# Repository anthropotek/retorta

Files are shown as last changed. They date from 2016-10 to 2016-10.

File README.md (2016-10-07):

# Retorta

mercury amalgam retort for gold mining

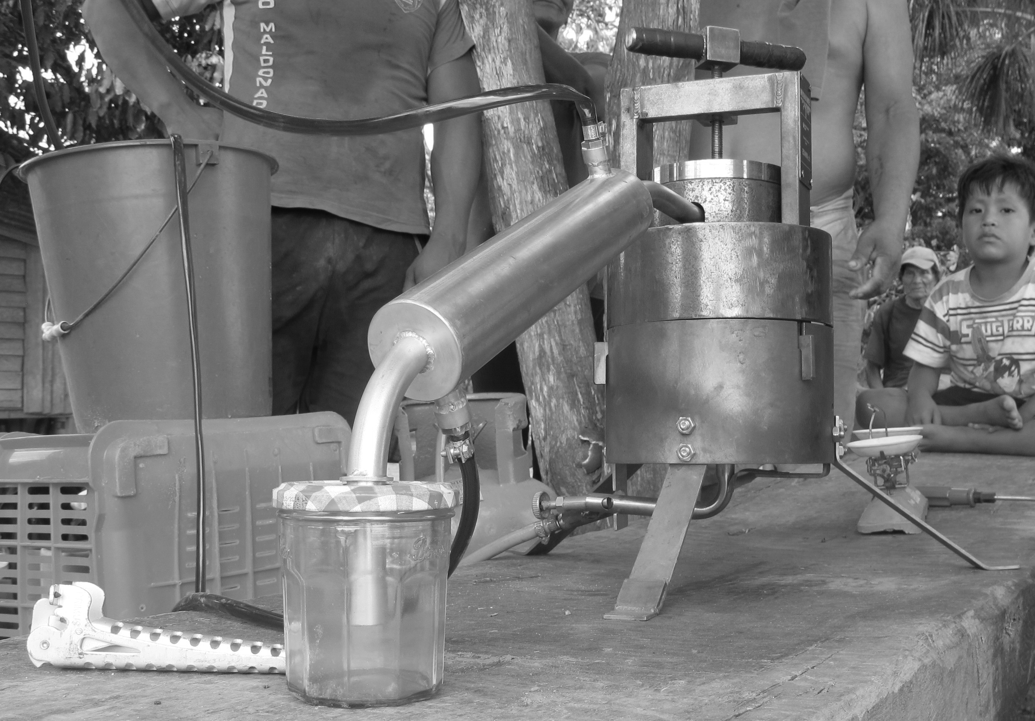
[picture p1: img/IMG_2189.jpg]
Retorta


## Getting Started

These instructions will get you a copy of the project up and running on your local machine for development and testing purposes. See deployment for notes on how to deploy the project on a live system.

### Prerequisities

What things you need to install the software and how to install them

```
Give examples
```

### Installing

A step by step series of examples that tell you have to get a development env running

Say what the step will be

```
Give the example
```

And repeat

```
until finished
```

End with an example of getting some data out of the system or using it for a little demo

## Running the tests

Explain how to run the automated tests for this system

### Break down into end to end tests

Explain what these tests test and why

```
Give an example
```

### And coding style tests

Explain what these tests test and why

```
Give an example
```

## Deployment

Add additional notes about how to deploy this on a live system

## Built With

* Dropwizard - Bla bla bla
* Maven - Maybe
* Atom - ergaerga

## Contributing

Please read [CONTRIBUTING.md](https://gist.github.com/PurpleBooth/b24679402957c63ec426) for details on our code of conduct, and the process for submitting pull requests to us.

## Versioning

We use [SemVer](http://semver.org/) for versioning. For the versions available, see the [tags on this repository](https://github.com/your/project/tags). 

## Authors
Haute Ecole Arc Engineering - Team "User-Centered Product Design", website: http://anthropotechnologie.org/
This hardware is part of Wanamei project, focusing on developing socio-technical solutions to improve current mining problematics, website of the project: http://wanamei.org/

## License

This project is licensed under the Creative Commons Licence – Attribution Non commercial – ShareAlike 3.0 Unported. This means that the retorta cannot be marketed directly and in a collaborative spirit, we ask you to share with us the modifications you might have made. See the https://creativecommons.org/licenses/by-sa/3.0/ website for details.

## Acknowledgments

* Hat tip to anyone who's code was used
* Inspiration
* etc

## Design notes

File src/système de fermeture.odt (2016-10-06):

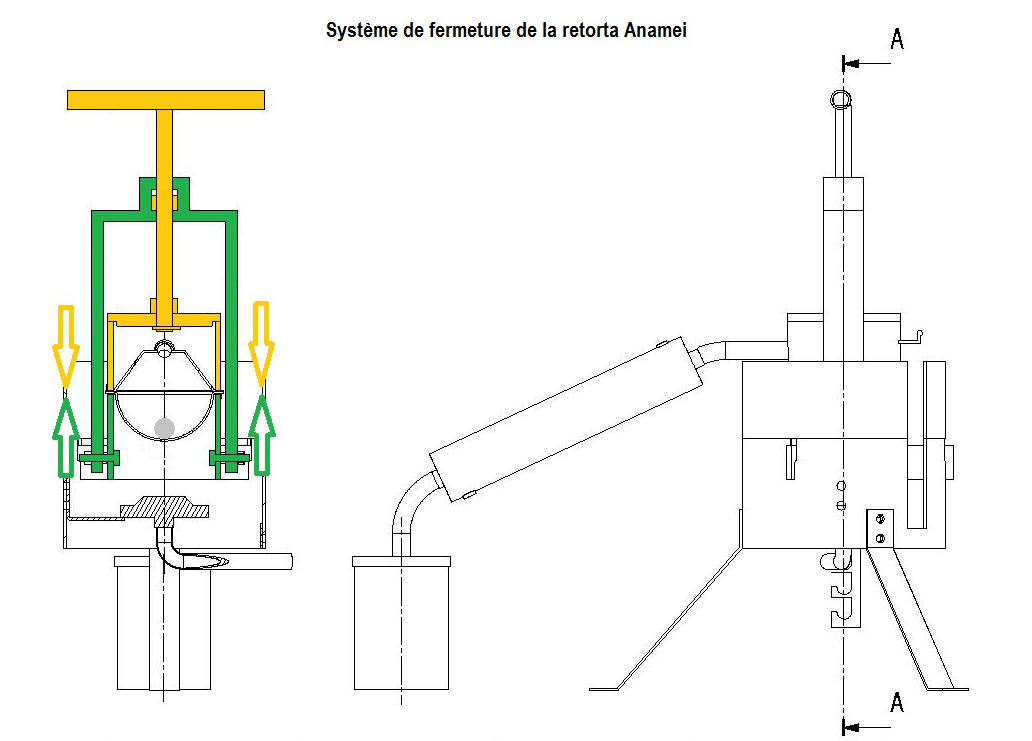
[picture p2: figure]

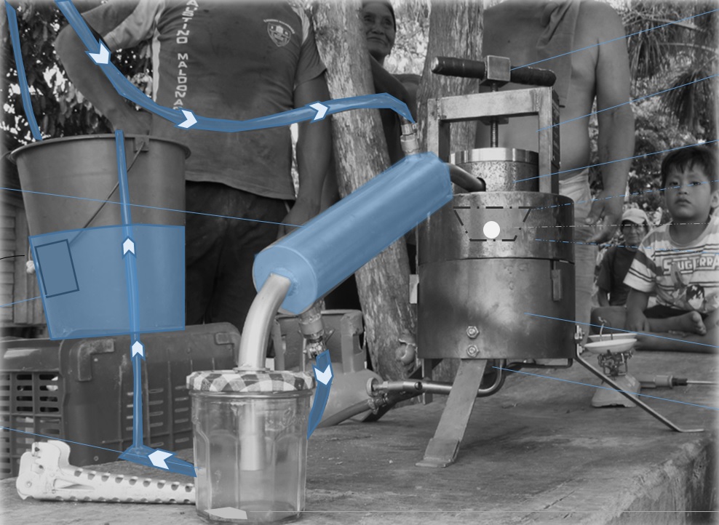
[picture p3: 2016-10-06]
img/IMG_2189 water.jpg

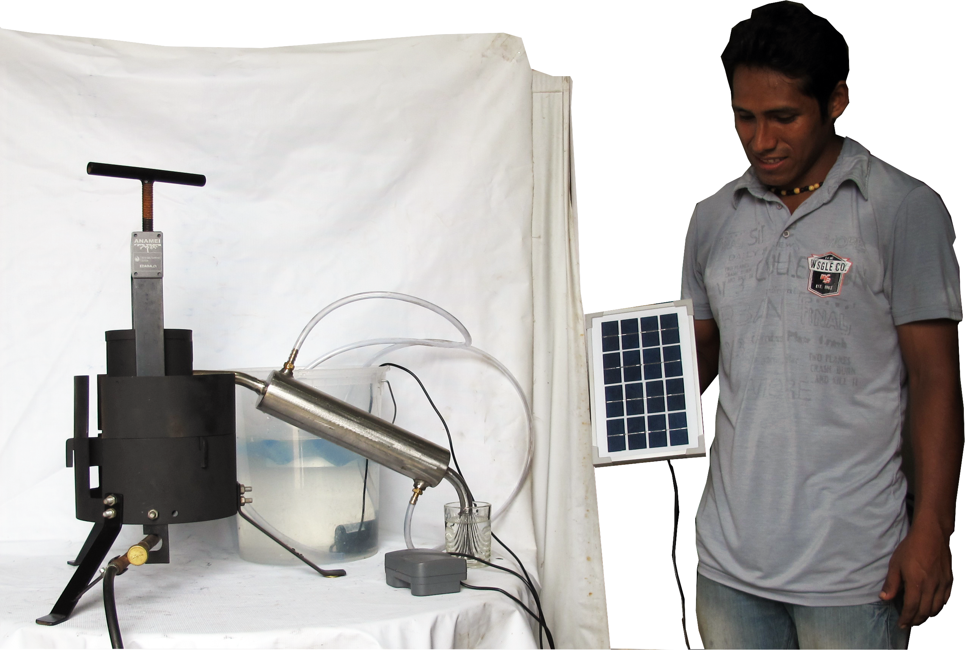
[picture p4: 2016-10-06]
img/retorta complete.png

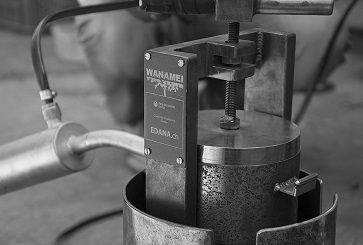
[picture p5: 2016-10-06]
img/DSC_0791pp.jpg

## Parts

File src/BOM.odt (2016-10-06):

Matériaux nécessaire à la fabrication

- Matériaux et dimensions nécessaires pour fabriquer la retorta:

Toutes les pièces sont en acier. Seul le refroidisseur est en acier inoxydable.

N° | Nom de la pièce | Photo | Matériau | Quantité
1 | Poignée | | Acier | Tube : longueur 180mm, Diamètre ext. 20mm, diamètre intérieur 10mm
2 | Tige filetée | | Acier – Degré 8 | Tige filetée : longueur 230mm, diamètre 16mm
3 | Bras | | Acier | Profil rectangulaire : 10mm*40mm, longueur : 700mm
4 | Couvercle en acier | | Acier | Plaque circulaire : diamètre 121mm, épaisseur 10mm
5 | Tube supérieur | | Acier laminé à chaud | Tube à parois épaisses, sans soudure : diamètre extérieur 121mm, diamètre intérieur 101mm, longueur 70mm
6 | Couvercle inox/ Refroidisseur inox | | Acier inoxydable 304 | Tube extérieur : diamètre extérieur 51mm, diamètre intérieur : 47mm Tube intérieur : diamètre 18mm, diamètre intérieur 16mm Plaque pour le couvercle : 600mm*185mm, épaisseur 2mm
7 | Récipient | | Aluminium / Acier inoxydable 304 | Diamètre extérieur : 120mm, rebord de 10mm, hauteur de 60mm
8 | Tube inférieur | | Acier laminé à chaud | Tube à paroi épaisse, sans soudure : diamètre extérieur 121mm, diamètre intérieur 101mm, longueur 87mm
9 | Carapace/ Armature | | Acier | Plaque de 600mm*185mm, épaisseur 3mm
10 | Pieds (*3) | | Acier | Plaque de 90mm*224mm, épaisseur 3mm (pour les 3 pieds)
11 et 12 | Supports bruleur | | Acier | Plaque de 30mm*60mm

- Type de matériau

Pour le couvercle inox/Refroidisseur inox : il est recommandé d’utiliser l’acier inoxydable AISI 304. L’inox permet de récupérer du mercure propre, non altéré ; la spécificité du n°304 est qu’il résiste aux fortes températures.

Pour les tubes supérieur et inférieur : il est recommandé d’utiliser du tube à parois épaisses, sans soudure, laminé à chaud de type : St 52.0, DIN 2448, DIN 1629.

Pour les autres pièces: il est recommandé d’utiliser de l’acier standard.

30.07.2015 wanamei.wordpress.com Guide de fabrication - Retorta Anamei

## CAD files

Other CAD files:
src/Bague stop.CATPart
src/Bol.CATPart
src/Bruleur5.CATPart
src/Couvercle bol.CATPart
src/Couvercle.CATPart
src/Cuve.CATPart
src/Echappement Retorta.CATProduct
src/Refroidisseur.CATPart
src/RetortaVF.CATProduct
src/RetortaVF2.CATProduct
src/barre.CATPart
src/carapace3.CATPart
src/carapace3_haut.CATPart
src/couvercle retorta.CATPart
src/ecrou hexa M8.CATPart
src/ecrou hexa.CATPart
src/embout 1.CATPart
src/embout 2.CATPart
src/goupille.CATPart
src/nouvel arceau.CATPart
src/pied3.CATPart
src/poignee .CATPart
src/support bruleur.CATPart
src/support soude bruleur.CATPart
src/tube bas2.CATPart
src/tube haut.CATPart
src/tube.CATPart
src/vis hexa M8 L35.CATPart

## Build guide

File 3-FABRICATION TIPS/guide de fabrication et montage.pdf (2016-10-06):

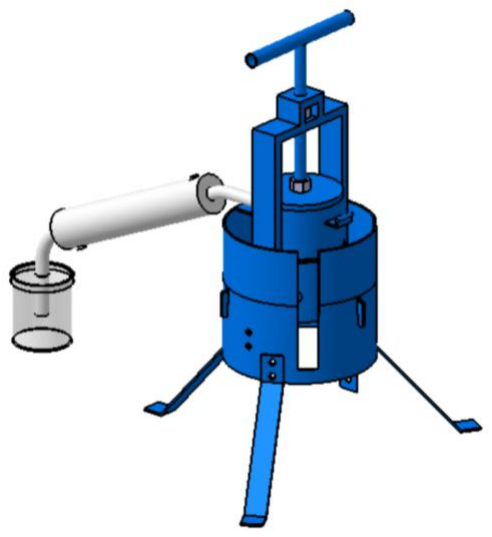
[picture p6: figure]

30.07.2015 | wanamei.wordpress.com | Guide de fabrication - Retorta Anamei

# Retorta Anamei

# Guide de fabrication et de montage

## Plan de montage

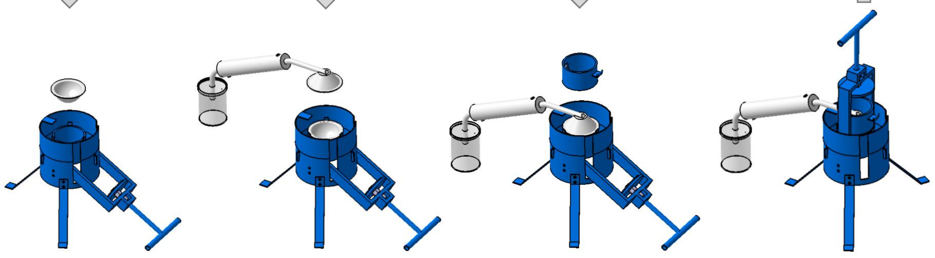
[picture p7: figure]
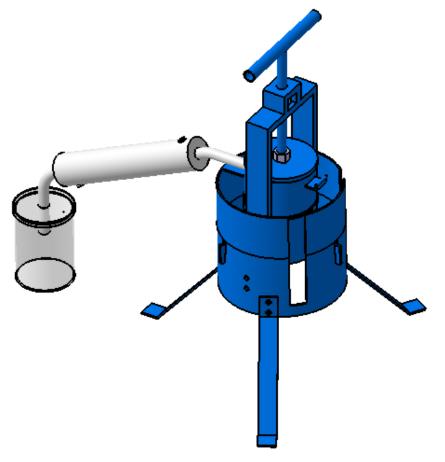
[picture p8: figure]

## Eléments de la retorta

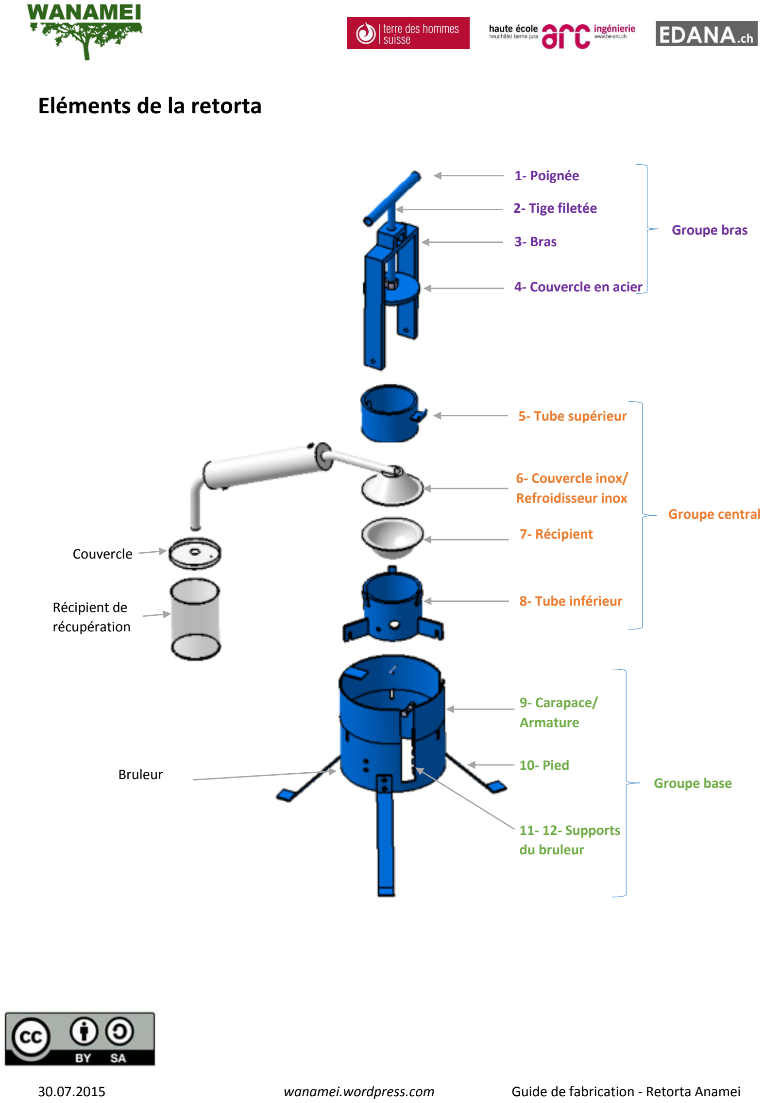
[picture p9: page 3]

Bruleur

9- Carapace/
Armature

10- Pied

Récipient de
récupération

6- Couvercle inox/
Refroidisseur inox

1- Poignée

4- Couvercle en acier

3- Bras

5- Tube supérieur

7- Récipient

8- Tube inférieur

11- 12- Supports
du bruleur

2- Tige filetée
Groupe bras

Couvercle

Groupe central

Groupe base

## Indications générales pour la fabrication

- Groupe base

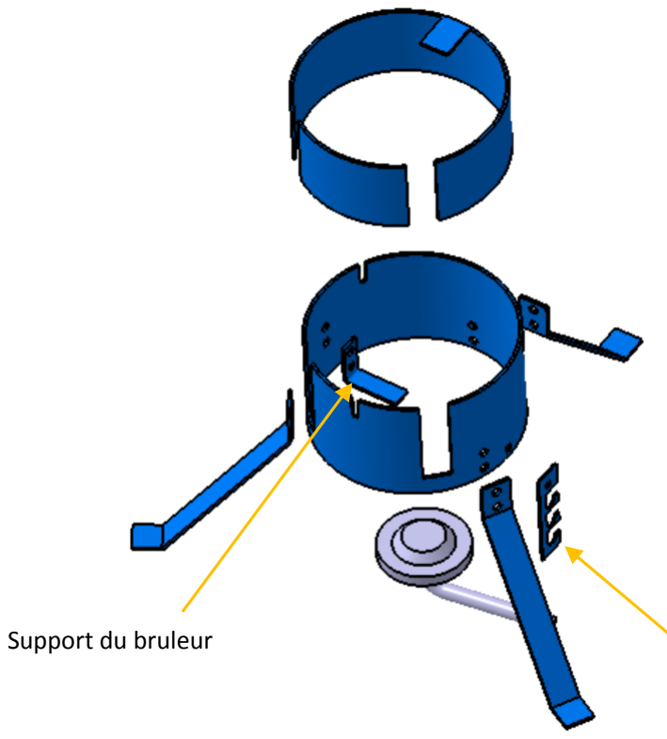
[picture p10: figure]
Support du bruleur

9 vis M8 – Longueur 16
9 écrous M8

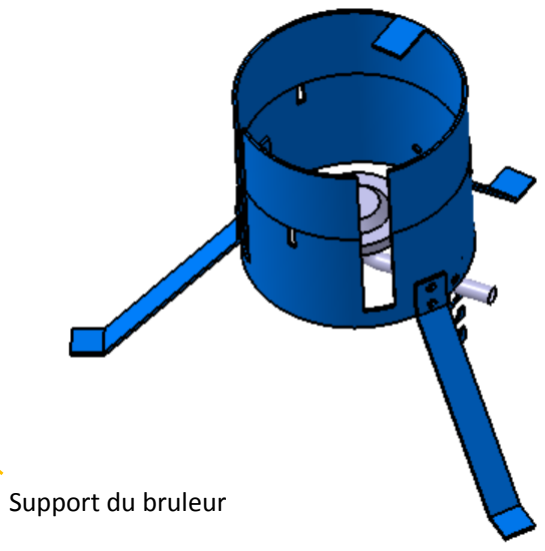
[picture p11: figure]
Support du bruleur
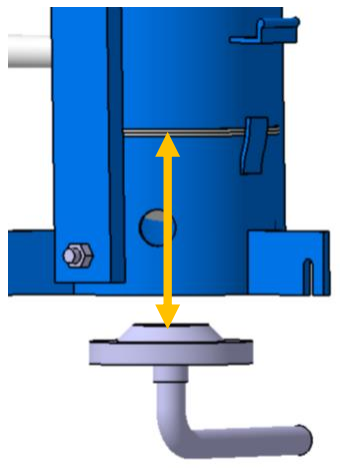
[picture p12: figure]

Distance entre le bruleur et le récipient: 90 à 100mm

- Groupe central

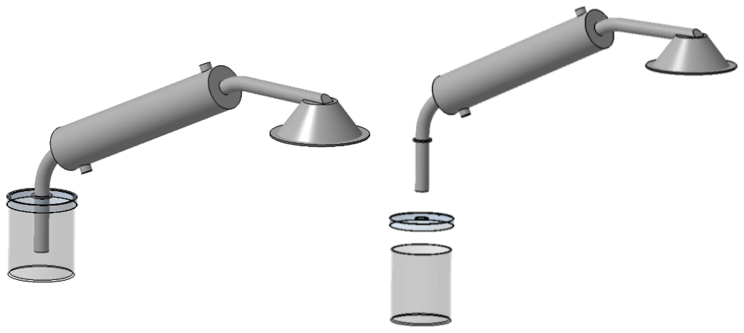
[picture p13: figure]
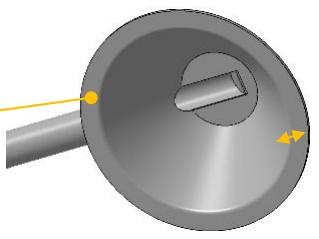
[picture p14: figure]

Notes pour la fabrication :

- Acier inoxydable 2mm d’épaisseur
- Soudure TIG
- Cette surface doit être lisse
- La largeur du rebord doit mesurer 9 mm (minimum)
- Les soudures doivent être faite à l’extérieur du couvercle.
- Cet angle doit être respecté.

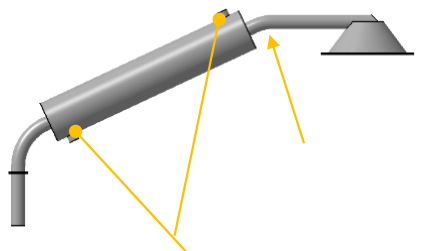
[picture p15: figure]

- Le pas de vis pour fixer les 2 connecteurs hydrauliques est : ¼.

Pour connaitre toutes les précautions de fabrication concernant la fabrication de cette pièce : voir le document « fabrication du refroidisseur » sur www.wanamei.org. (http://www.wanamei.orf/)

1 verre transparent – hauteur:135mm Trou de diamètre 18mm

9 mm

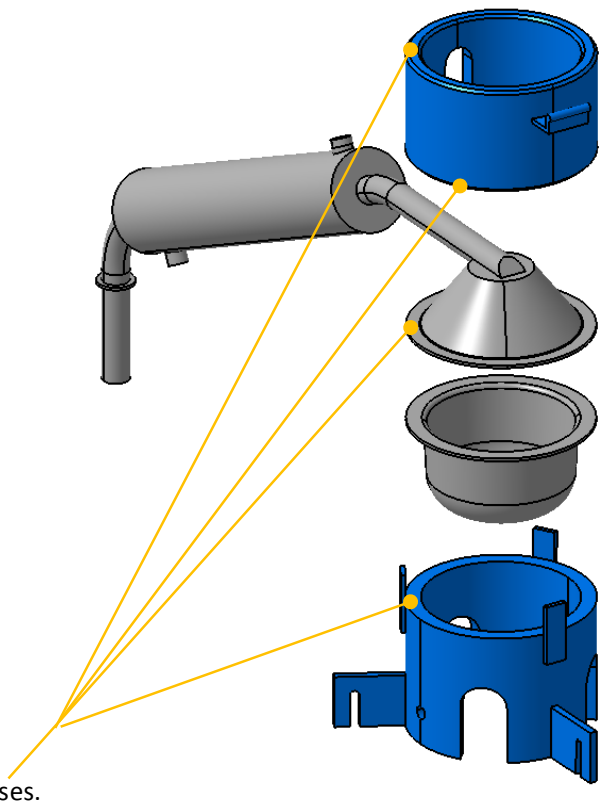
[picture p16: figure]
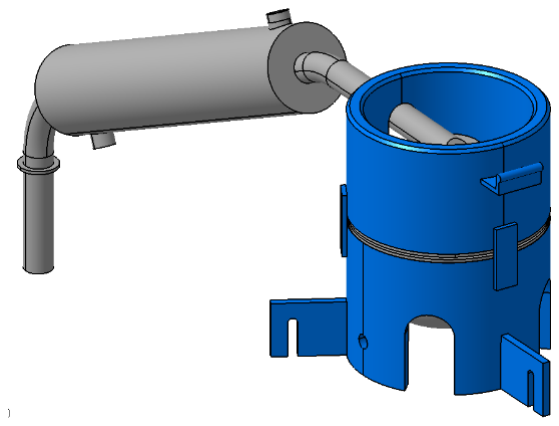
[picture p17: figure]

- Les surfaces de ces tubes doivent être bien lisses.
- Les deux tubes à parois épaisses sont acier sans sandure, laminé à chaud.
- Il est important que ces deux trous soient alignés (l’un en face de l’autre), car ils servent à la rotation du bras.

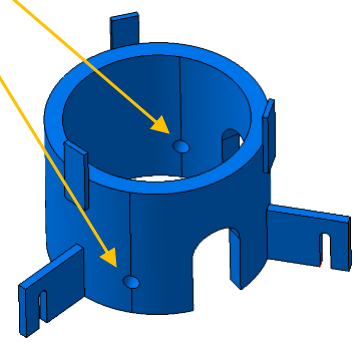
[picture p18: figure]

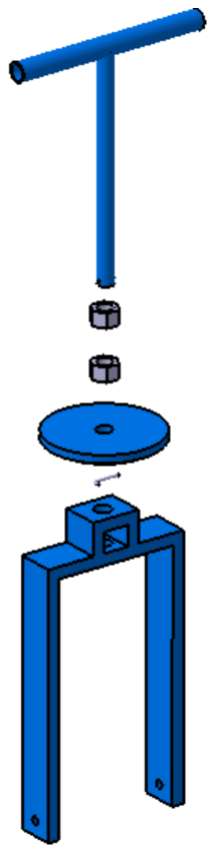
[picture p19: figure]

- Groupe bras

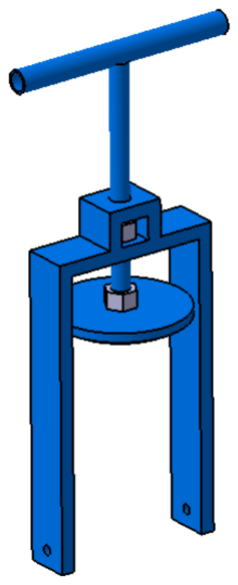
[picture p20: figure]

- Fixation du bras sur le tube inférieur :

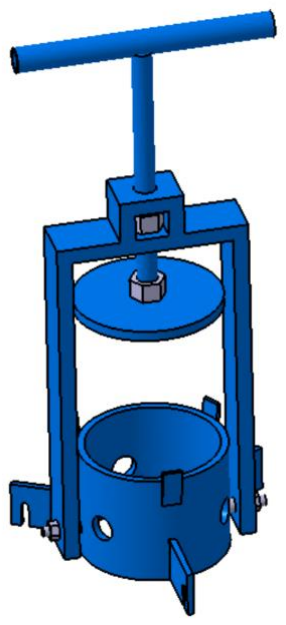
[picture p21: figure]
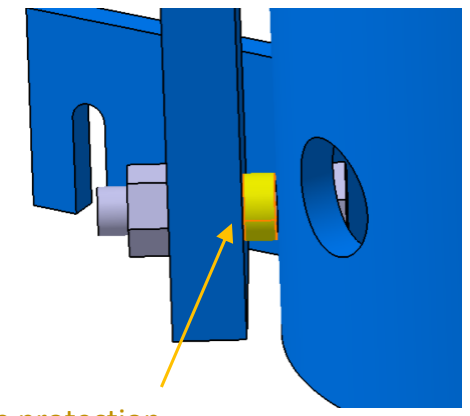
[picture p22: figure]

Pour plus d’informations sur la fabrication de la retorta voir la vidéo : « Fabricación de la retorta Anamei » sur www.wanamei.org. (http://www.wanamei.orf/)

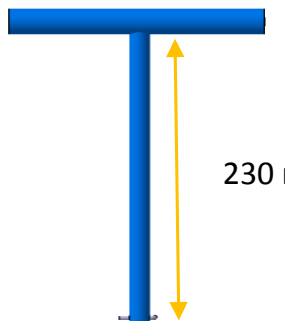
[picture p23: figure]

1 tige filetée : diamètre 16mm, longueur 230 mm

2 écrous de diamètre 16mm

1 goupille de diamètre 2.5 mm

2 vis M8 – Longueur 35mm + 2 écrous M8
2 tubes de protection : Diamètre intérieur 8.2mm, diamètre exterieur 11mm

230 mm

Tubes de protection

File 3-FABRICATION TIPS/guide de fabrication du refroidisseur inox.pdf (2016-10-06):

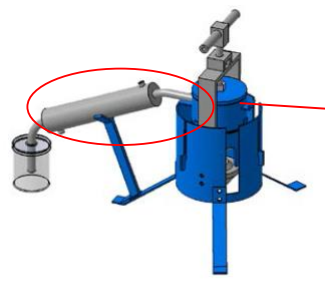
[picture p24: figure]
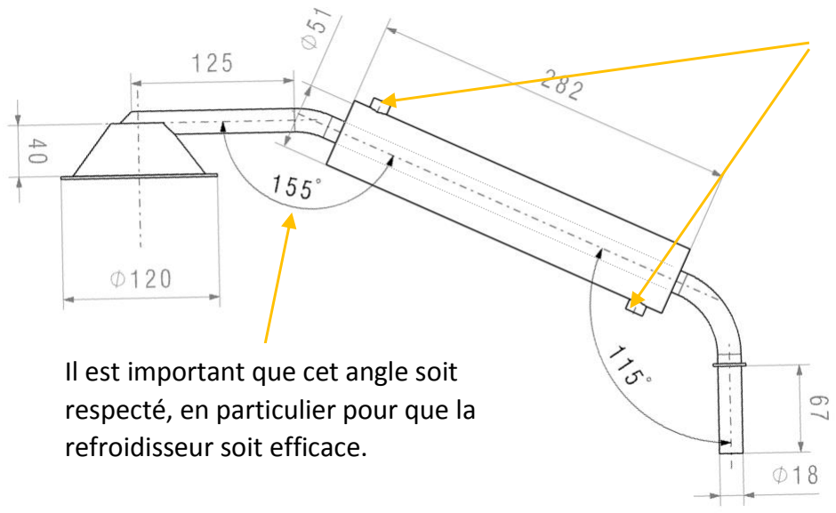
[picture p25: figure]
Il est important que cet angle soit respecté, en particulier pour que la refroidisseur soit efficace.

07.10.2014

## Fabrication de la retorta Anamei

## Précautions de fabrication pour le refroidisseur Inox

Le refroidisseur est la partie de la retorta dans laquelle les vapeurs de mercure se condensent grâce à la circulation d’eau froide.

Matériau:

Il recommandé, pour cette pièce, d’utiliser l’acier inoxydable AISI 304. L’inox permet de récupérer du mercure propre, non altéré ; la spécificité du n°304 est qu’il résiste aux fortes températures.

Dimensions (en mm)

Les pas de vis pour l’entrée et la sortie d’eau sont : ¼.

Sortie du mercure

Couvercle Refroidisseur

Patrons nécessaires à la fabrication du couvercle:

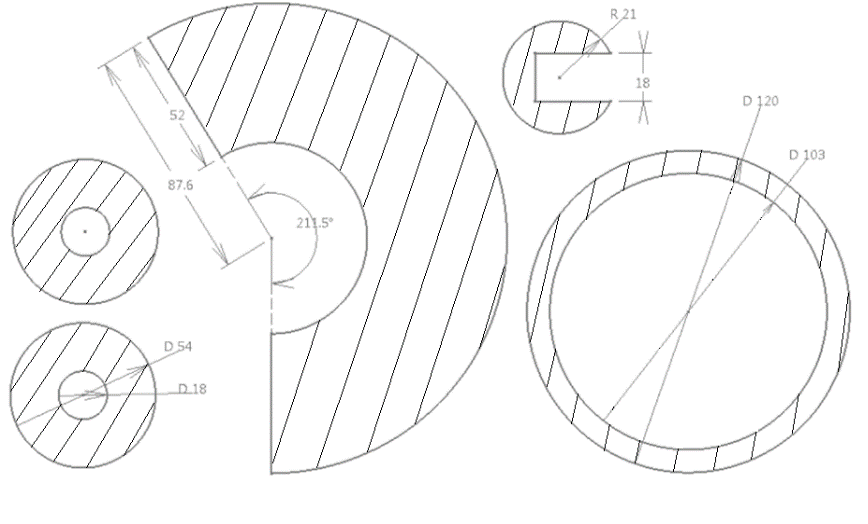
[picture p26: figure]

Attention lors de la fabrication!

L’étanchéité de la retorta dépend particulièrement de la fabrication de cette pièce.

Pour que la retorta soit bien étanche, il est très important de respecter les points suivants pour la fabrication du refroidisseur :

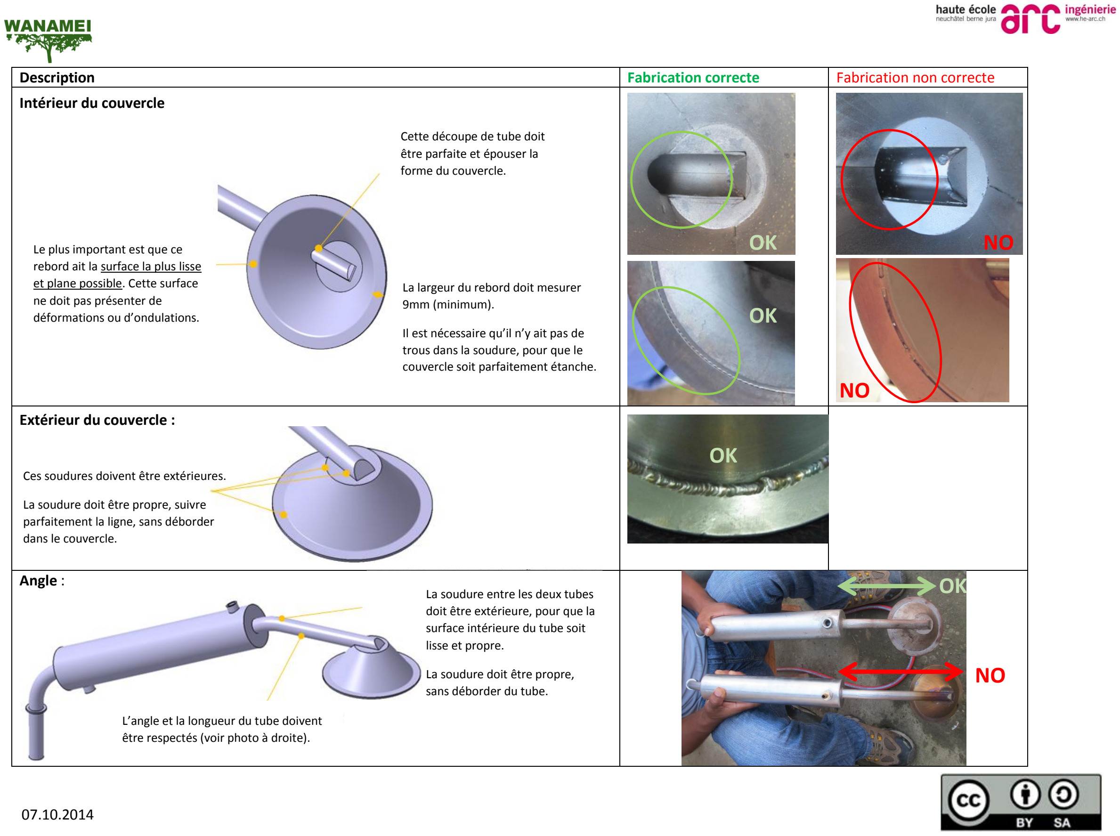
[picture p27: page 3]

Description | Fabrication correcte | Fabrication non correcte
Intérieur du couvercle
Extérieur du couvercle : Ces soudures doivent être extérieures. La soudure doit être propre, suivre parfaitement la ligne, sans déborder dans le couvercle. | OK
Angle : La soudure entre les deux tubes doit être extérieure, pour que la surface intérieure du tube soit lisse et propre. La soudure doit être propre, sans déborder du tube. L’angle et la longueur du tube doivent être respectés (voir photo à droite). | OK NO

OK

OK

NO

NO

Cette découpe de tube doit être parfaite et épouser la forme du couvercle.

La largeur du rebord doit mesurer 9mm (minimum).

Il est nécessaire qu’il n’y ait pas de trous dans la soudure, pour que le couvercle soit parfaitement étanche.

Le plus important est que ce rebord ait la surface la plus lisse et plane possible. Cette surface ne doit pas présenter de
déformations ou d’ondulations.

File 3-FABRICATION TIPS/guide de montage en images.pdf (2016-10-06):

### Montage de la retorta Anamei – En images…

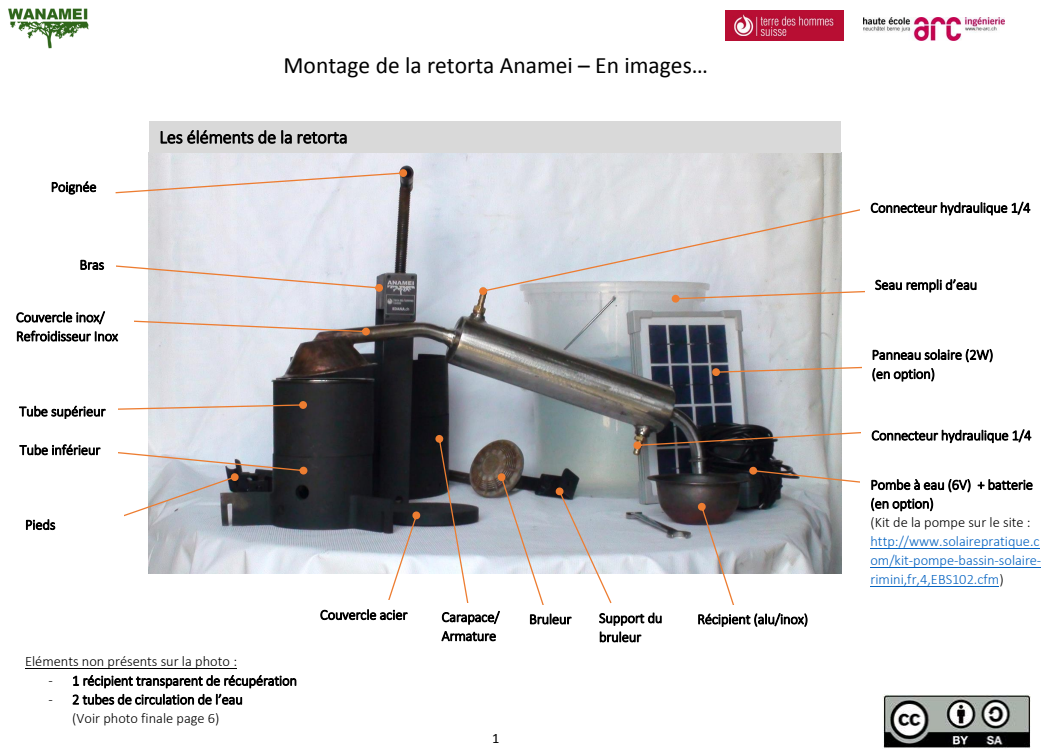
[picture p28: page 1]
Poignée; Bras; Couvercle inox/ Refroidisseur Inox; Tube supérieur; Tube inférieur; Pieds; Couvercle acier; Carapace/; Armature; Bruleur; Support du; bruleur; Connecteur hydraulique 1/4; Panneau solaire (2W) (en option)

Les éléments de la retorta

Seau rempli d’eau

Pombe à eau (6V) + batterie
(en option)
(Kit de la pompe sur le site :
http://www.solairepratique.c
om/kit-pompe-bassin-solaire-
rimini,fr,4,EBS102.cfm) (http://www.solairepratique.com/kit-pompe-bassin-solaire-rimini,fr,4,EBS102.cfm)

Récipient (alu/inox)

Eléments non présents sur la photo :
- 1 récipient transparent de récupération
- 2 tubes de circulation de l’eau
(Voir photo finale page 6)

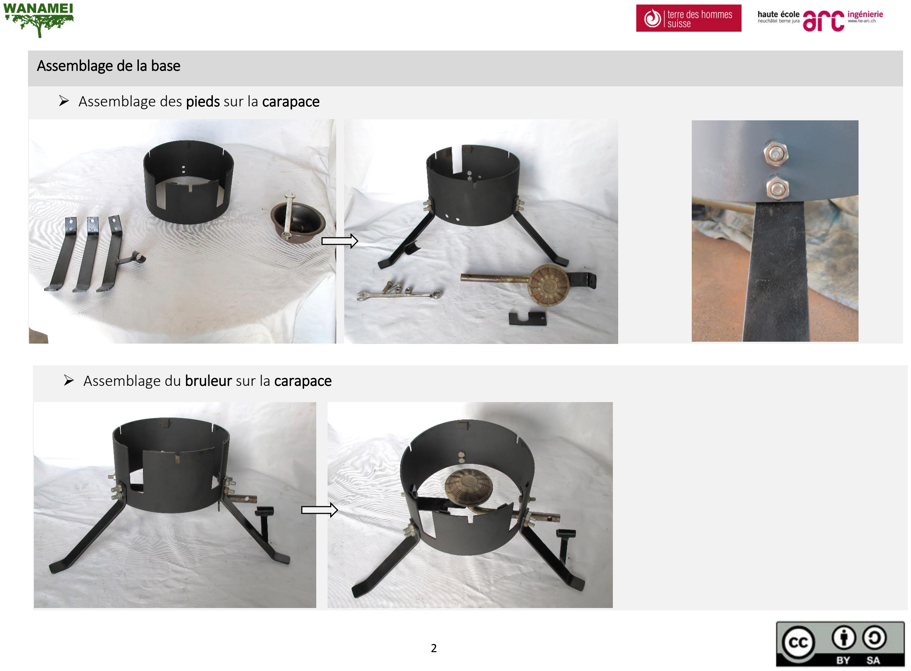
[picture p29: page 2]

- Assemblage du bruleur sur la carapace
- Assemblage des pieds sur la carapace

Assemblage de la base

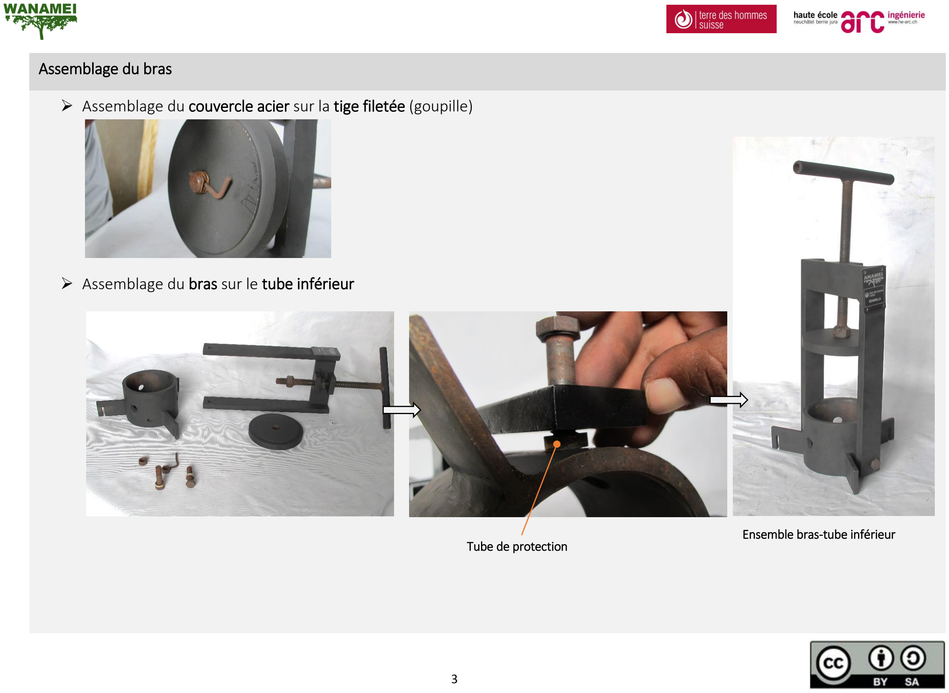
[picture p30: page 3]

- Assemblage du couvercle acier sur la tige filetée (goupille)
- Assemblage du bras sur le tube inférieur

Assemblage du bras

Tube de protection

Ensemble bras-tube inférieur

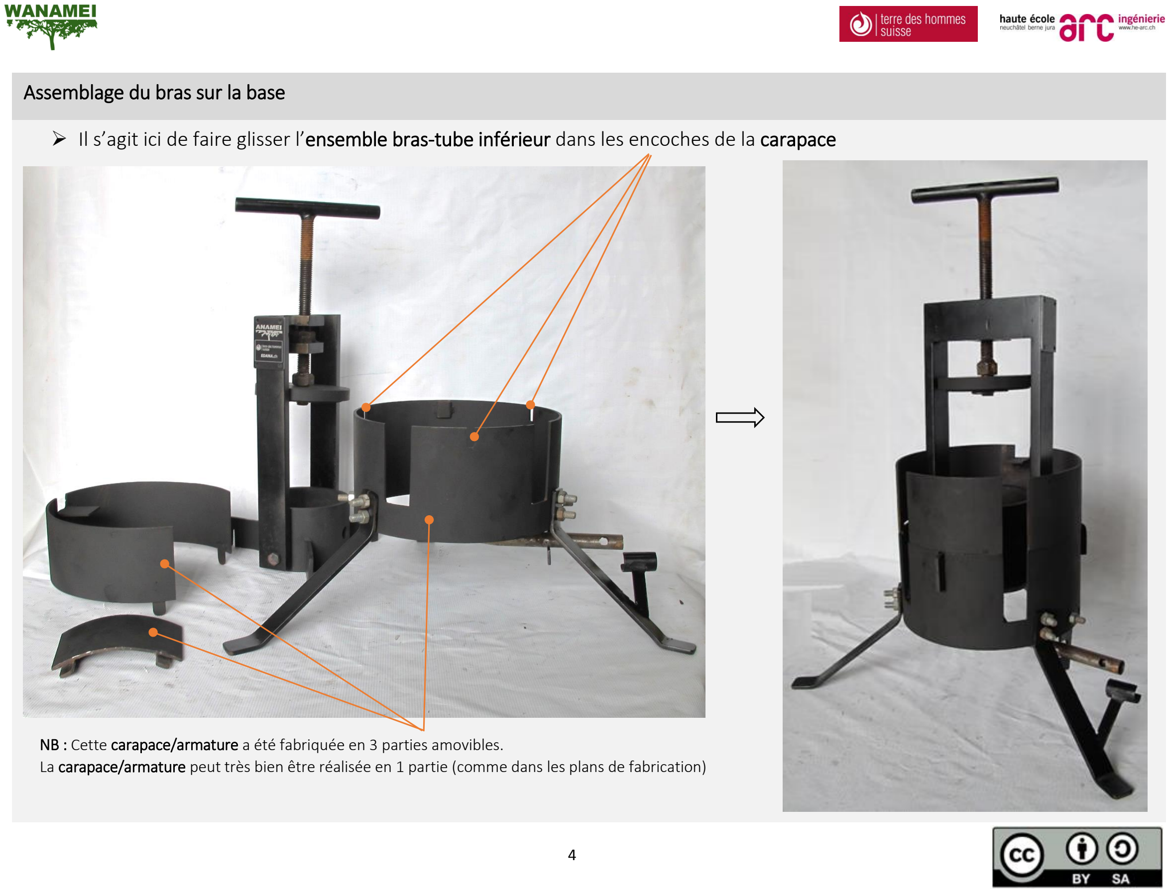
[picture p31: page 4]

- Il s’agit ici de faire glisser l’ensemble bras-tube inférieur dans les encoches de la carapace

Assemblage du bras sur la base

NB : Cette carapace/armature a été fabriquée en 3 parties amovibles.
La carapace/armature peut très bien être réalisée en 1 partie (comme dans les plans de fabrication)

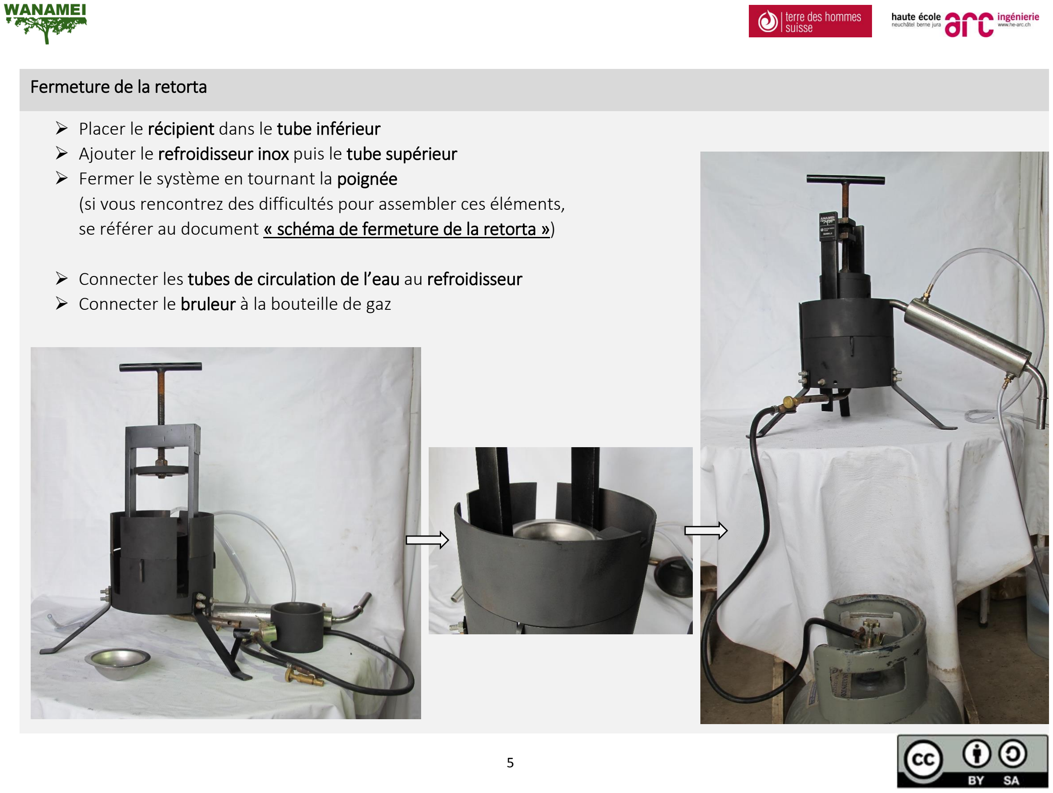
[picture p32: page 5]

- Placer le récipient dans le tube inférieur
- Ajouter le refroidisseur inox puis le tube supérieur
- Fermer le système en tournant la poignée
(si vous rencontrez des difficultés pour assembler ces éléments, se référer au document « schéma de fermeture de la retorta »)
- Connecter les tubes de circulation de l’eau au refroidisseur
- Connecter le bruleur à la bouteille de gaz

Fermeture de la retorta

La retorta est maintenant prête à être utilisée !

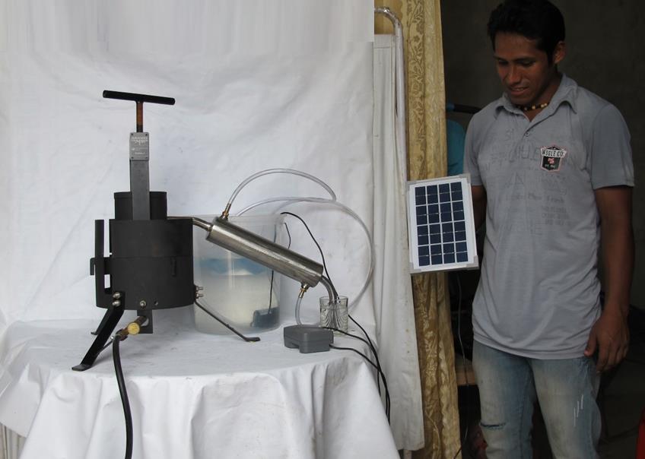
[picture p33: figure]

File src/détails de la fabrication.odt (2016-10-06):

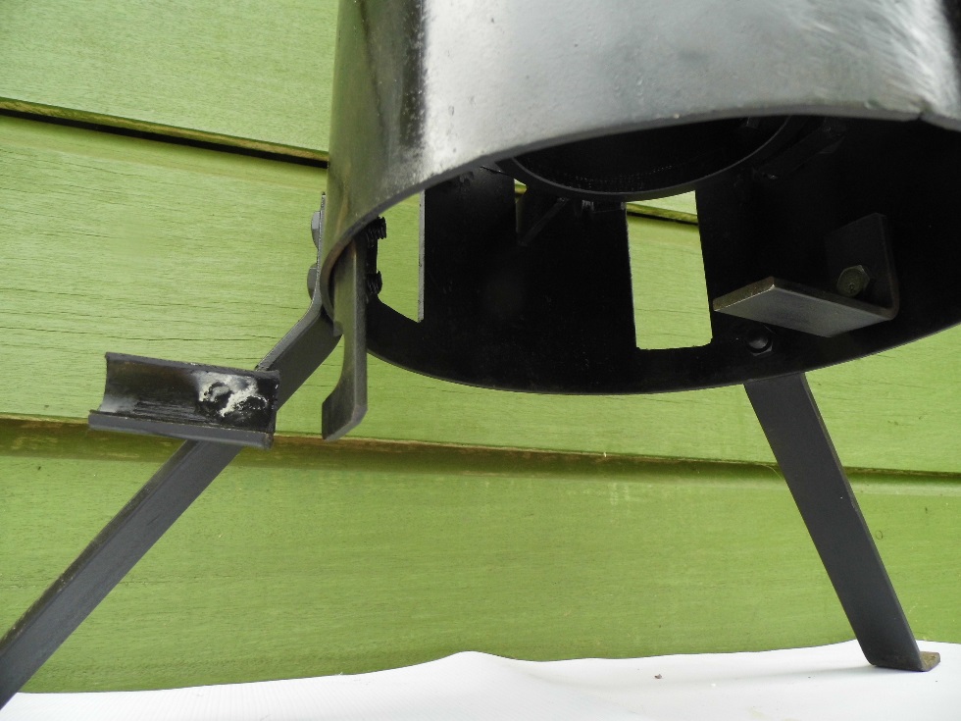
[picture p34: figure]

Quelques détails de la fabrication de la retorta Anamei – En images…

Détail du bras

Détail du support pour le bruleur

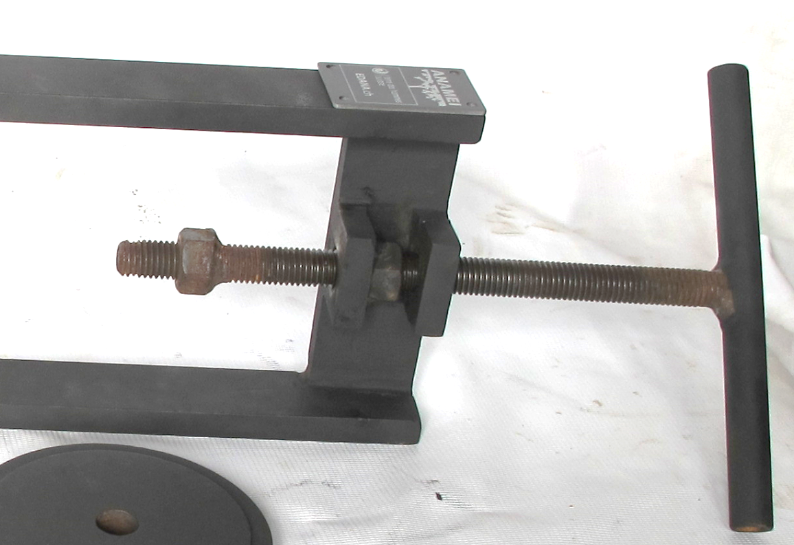
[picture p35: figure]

Différents types de récipients

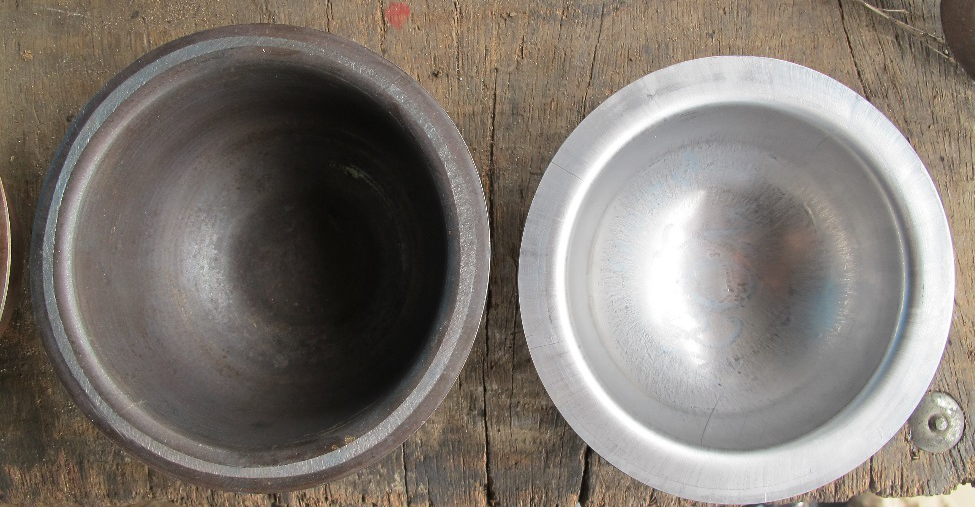
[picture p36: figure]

En aluminium

Soudés

Soudés

En inox 304

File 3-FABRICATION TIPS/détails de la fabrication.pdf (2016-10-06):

### Quelques détails de la fabrication de la retorta Anamei – En images…

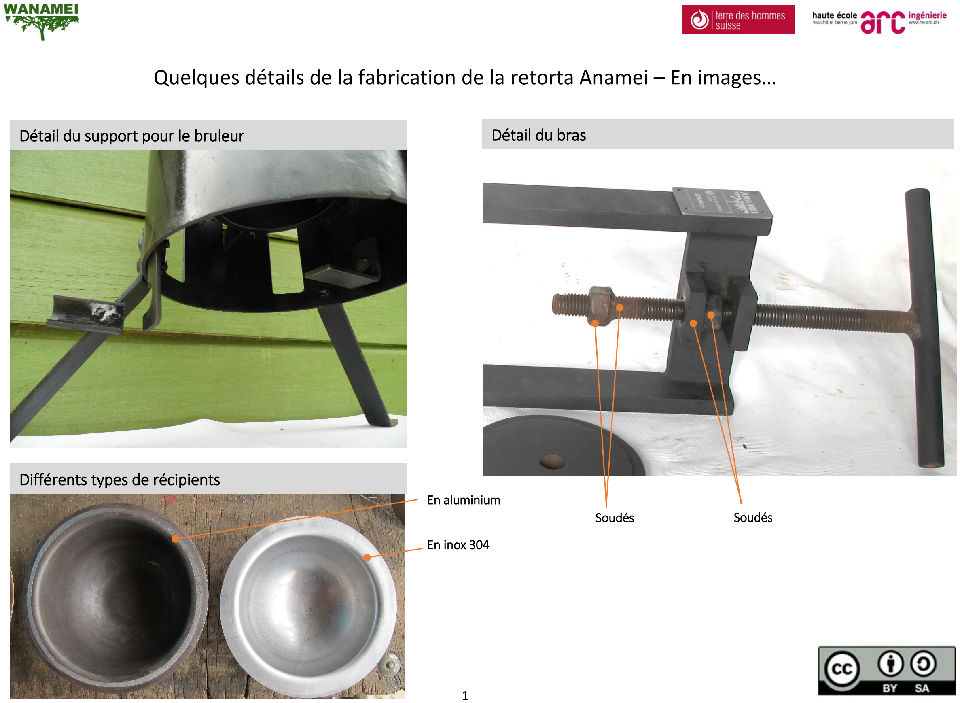
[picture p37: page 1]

1

Détail du support pour le bruleur | Détail du bras

Différents types de récipients

Soudés | Soudés

En aluminium

En inox 304

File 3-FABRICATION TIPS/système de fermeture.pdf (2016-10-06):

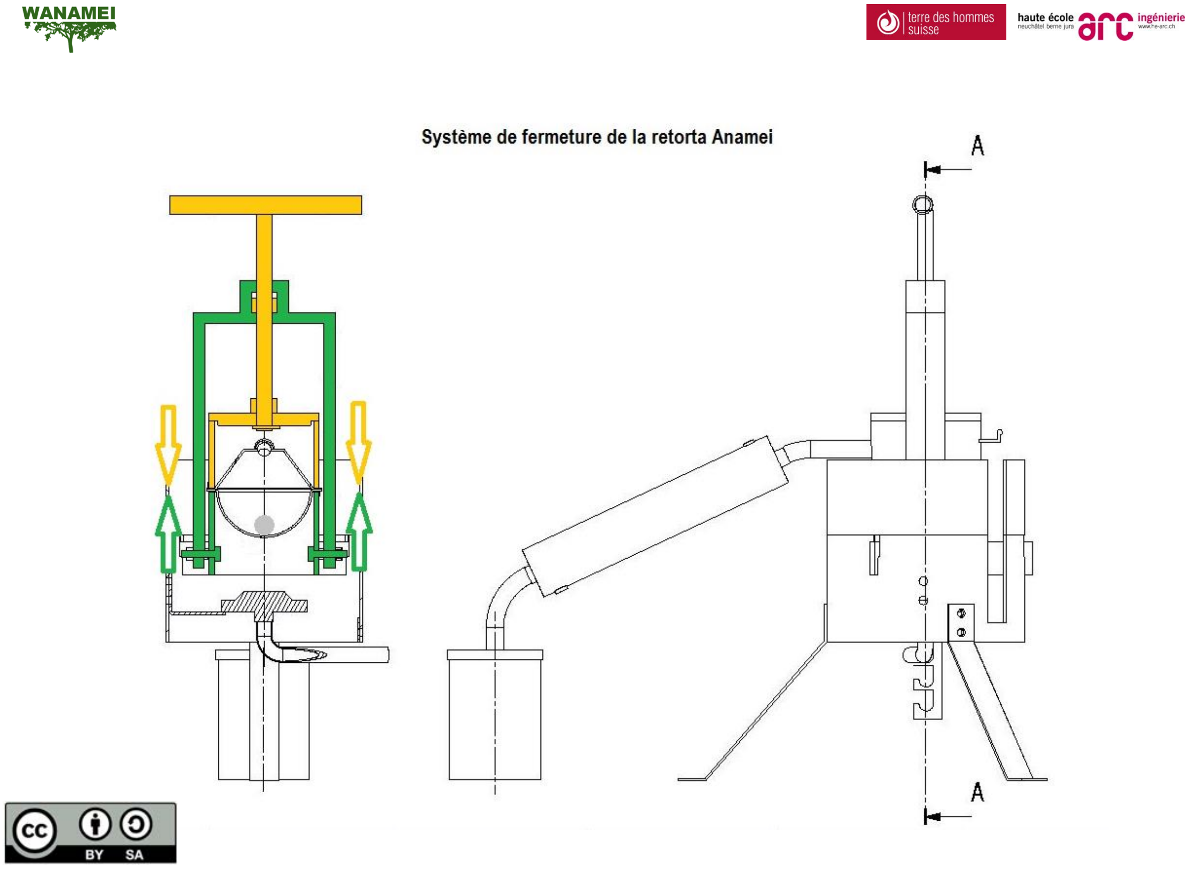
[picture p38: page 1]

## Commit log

2016-10-06 2016-10-06
    CAD file of the retort, .stl
2016-10-06 update documents
    [Bague stop.CATPart, Bol.CATPart, Bruleur5.CATPart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]
